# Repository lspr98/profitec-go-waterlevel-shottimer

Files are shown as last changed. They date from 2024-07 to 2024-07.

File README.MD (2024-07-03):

# Waterlevel-indicator and shot-timer for the Profitec GO

<p align="middle">
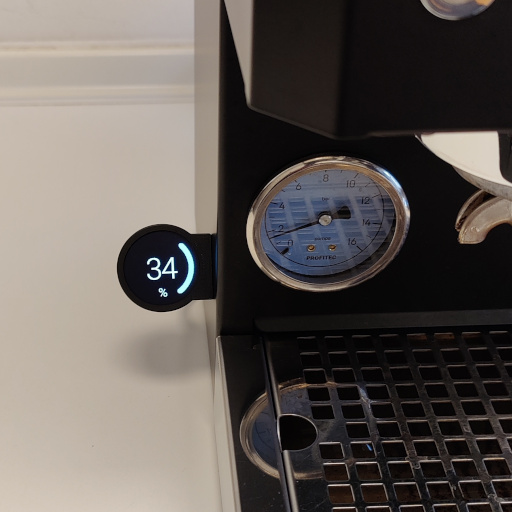
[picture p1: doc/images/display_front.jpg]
  
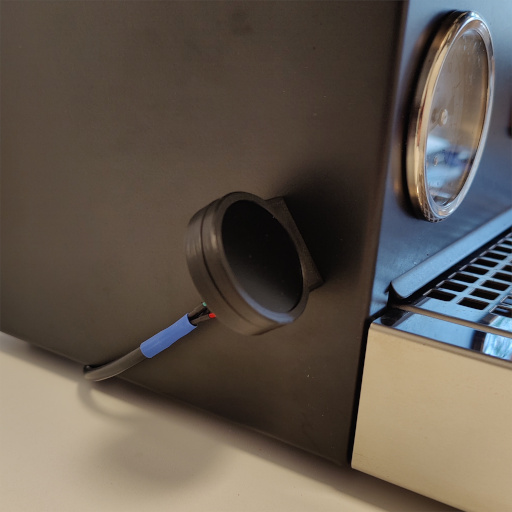
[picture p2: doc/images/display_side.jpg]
   
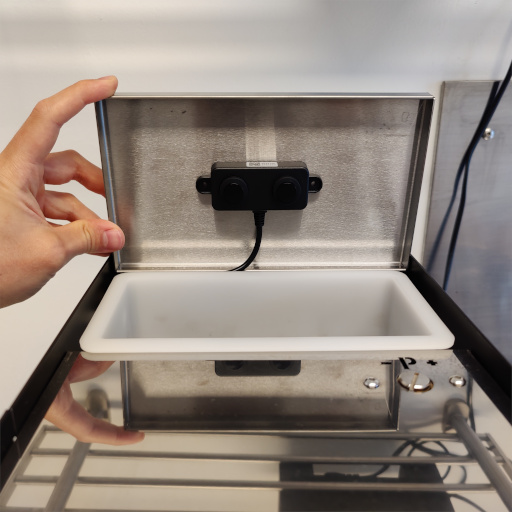
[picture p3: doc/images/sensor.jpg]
  
</p>

A modern display mod for espresso machines with vibrationpumps. Includes a shot-timer and waterlevel-indicator. Uses an accelerometer to detect vibrations for waking-up the display and timing shots. Measures and displays the waterlevel based on a contactless ultrasonic sensor. Attaches to the machine via a magnet for easy repositioning. The mod was originally developed and tested for the Profitec GO, however, other machines with vibrationpumps might work as well.

## Features
|Tap wake|Portafilter wake|Timer|
|---|---|---|
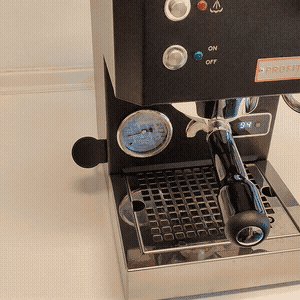
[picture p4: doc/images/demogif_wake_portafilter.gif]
||||

- contactless waterlevel measurement
- easy repositioning via magnetic attachment
- automatic wake when interacting with the machine
- automatic shot-timer
- non-destructive installation, minimal wiring outside the machine
- adjustable colors, sensitivity, etc...

## Disclaimer and warning
Recreating this project involves handling dangerous things like soldering irons, 3D-printers and mains voltage. For legal reasons, handling these things should only be done by an expert. I am not responsible for any damage to you, your machine or your surrounding. Read through the complete [manual](doc/manual/manual.pdf) to decide if you feel comfortable building the mod and if it is worth the effort to you.

## Required Tools
- 3D-printer
- soldering iron
- connector crimping kit (see BoM)

## Building Instructions
The building manual can be found [here](doc/manual/manual.pdf)

## Usage notes and configuration
I unfortunately don't have a second machine to test how well the settings transfer to different machines, so here are some hints on how to dial in things like detection sensitivity and timings. All relevent parameters (**highlighted in bold**) can be adjusted in [include/config.h](include/config.h). You need to reflash the firmware after making any changes. Refer to the manual on how to flash the firmware. **Never connect to the display via USB when the display cable is plugged in to avoid damage to your computer.** The 5V lines of the USB port and the display cable are connected!

### Adjusting vibration sensing sensitivity
The parameter for controlling vibration detection sensitivity is **WAKE_THRESH**. A lower value increases sensitivity, a higher value decreases sensitivity. The value has to be larger than 0. For different machines and mounting positions of the display, a different value for **WAKE_THRESH** may be required for reliable operation. The sensitivity affects both, the wake and timer function. A good value for **WAKE_THRESH** should wake the display when gently tapping on it and should keep the timer going reliably. My method of deciding on the threshold: you should be able to wake the display by slamming your fist on the surface on which the machine is standing on but it should not wake when placing a glass of water on that surface.

### Adjusting waterlevel and warning threshold
A fill level of 0 percent is shown if the sensor reports a distance of **LEVEL_MAX_DIST_MM** millimeters or more. A fill level of 100 percent is shown if the sensor reports a distance of **LEVEL_MIN_DIST_MM** millimeters or less. You can configure these two values to account for different watertank depths. The percentage below which the color of the ring will change to orange is configured with **LEVEL_BAD_PERC**.

### Shottimer
The shottimer is displayed with a delay of two seconds, which is on purpose. When a vibration is detected, the system will timeout for two seconds and check for a vibration after that timeout. If there is still a vibration, the timer starts (taking into account the time passed during the timeout). This is done to prevent the timer activating every time someone interacts with the machine. The delay can be configured via **TIMER_TRIGGER_DELAY_MS**. Setting this to zero will start the timer instantly when the display is awake and some vibration is detected. There is also the option to adjust *how many milliseconds one timer second has* via **TIMER_INCREMENT_MS**. I noticed that the timer on my machine seems to count a bit faster than a full second and verified that with the stopwatch of my smartphone. So you have that option to sync it with your machine timer.

### Deactivating waterlevel function or timer function
If you do not need the waterlevel but want the timer function, the system can be used without plugging in any levelsensor. The default wakescreen will be an orange ring with a questionmark, indicating a missing sensor. If you don't want the shottimer function, you can deactivate it by setting **ENABLE_TIMER** to false.

## Bill of materials (BoM)

The following items are necessary to build the waterlevel indicator. Items marked with a (*) at the beginning do not need to be the exact listed item but may be replaced with something else. Sourcing links are included for people based in germany (those are the shops where I got the items from).

|Item|Amount|Description|Comment|Sourcing (DE)|
|---|---|---|---|---|
|Waveshare RP2040-LCD-1.28|1|3-in-1 display, IMU and microcontroller|-|[BerryBase](https://www.berrybase.de/rp2040-mcu-board-1-28-zoll-runde-lcd-beschleunigungssensor-und-gyroskop)|
|DFRobot A02YYUW|1|waterproof ultrasonic sensor to measure waterlevel|-|[BotLand](https://botland.de/ultraschall-abstandssensoren/15717-ultraschall-abstandssensor-a02yyuw-3-450cm-wasserdicht-dfrobot-sen0311-5904422377984.html)|
|4-core wire|~1m|wire between display, sensor and power supply|I recommend using any old USB cable which you don't need anymore. For the Profitec Go, the wire diameter has to be smaller than 6mm to fit through one of the holes in the bottom of the machine!|-|
|M3 screw|1|required to screw the two 3D-printed parts together|12mm length|-|
|M3 Nut|1|required to secure the M3 screw|-|-|
|*Meanwell LPV-20-5|1|power supply to convert mains voltage to 5V|any small 5V power supply capable of delivering more than 0.5W should work, make sure they have fault-protection and have sufficient IP classification. This one is overkill with 15W but leaves headroom for future mods|[Reichelt](https://www.reichelt.de/led-trafo-15-w-5-v-dc-3000-ma-mw-lpv-20-5-p185792.html?&trstct=pos_14&nbc=1)|
|*Disc neodym magnet 12mm x 5mm|1|-|a smaller magent also works as long as it is strong enough. The magnet compartment is 12mm in diameter and 5mm high.|[Maqna](https://www.maqna.de/neodym-scheibenmagnet-13x5mm-vernickelt-grade-n45)|
|*Tesa Powerbond doublesided tape|~15cm|used for mounting the ultrasonic sensor and 5V power supply to the machine|other doublesided tape works too, make sure it has some thickness to it, since the bottom surface of the sensor is slightly recessed|[Hornbach](https://www.hornbach.de/p/tesa-powerbond-montageband-ultra-strong-1-5m-x-19mm/8643115/)|
|*Dupont 2-Pin Male and Female connectors|2|connects the display unit to the sensor and power supply|4x 1-pin is also possible. Only the 1-pin and 2-pin connectors fit through the holes in the bottom of the Profitec GO (~6mm diameter). Note: the linked product includes the required crimping tools and also the JST-XH connectors listed next|[Amazon](https://www.amazon.de/SOMELINE%C2%AE-Crimpzange-Stecker-JST-XH-EI-Serie/dp/B0C8N8JBDC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)|
|*JST-XH 4-Pin Male and Female connectors|2|connectors for display unit and sensor unit|other 4-pin connectors are also possible, but the 3D-printed parts are designed to house a JST-XH 4-Pin Female port.|see Dupont connectors|
|*JST-XH 2-Pin Male and Female connectors|1|connector for wiring harness and power supply|other 2-pin connectors are also possible|see Dupont connectors|
|*Wago 221-413 splicing connector|2|used to hook into the 230V line and connect the 5V power supply|it is also possible to instead build Y-splitters with connectors that are compatible with your machine to have a non-destructive installation|[Hornbach](https://www.hornbach.de/p/wago-221-413-compact-verbindungsklemme-0-14-4mm-3-leiter-hebelklemme-12-stueck/10593116/)|

Apart from the items listed above, you will need common consumables like **shrink tubing, solder and 3D-printer filament**.

It is also possible to connect the display, sensor and power supply by directly soldering the wires together if you do not want to buy and crimp any connectors. In this case, you won't be able to detach the display or sensor without cutting the wires.

### Support me
If you want to give something back, you can download the **.stl** models for 3D-printing from my [Printables project](https://www.printables.com/de/model/931582-profitec-go-waterlevel-indicator-with-shot-timer) to help me fill my Prusameters. Thank you :)

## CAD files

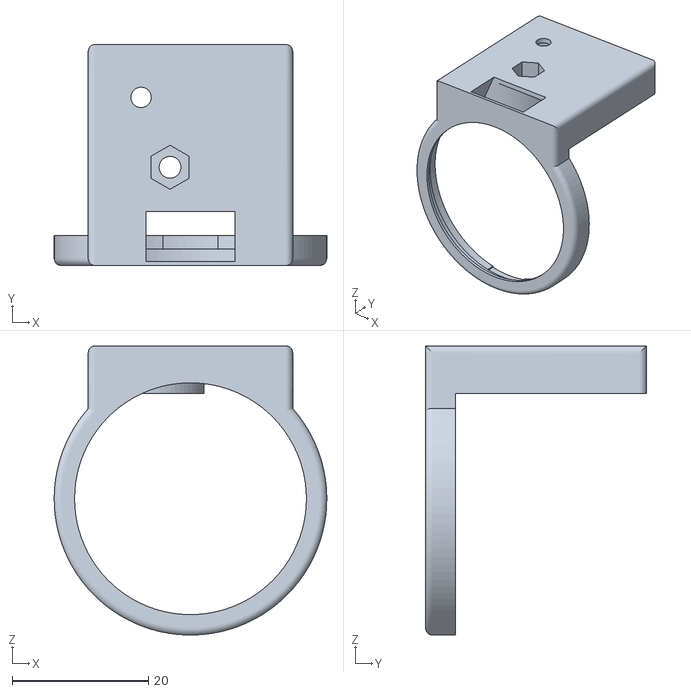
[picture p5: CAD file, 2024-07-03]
hardware/Frame v14.stl
40.0 x 32.4 x 42.4

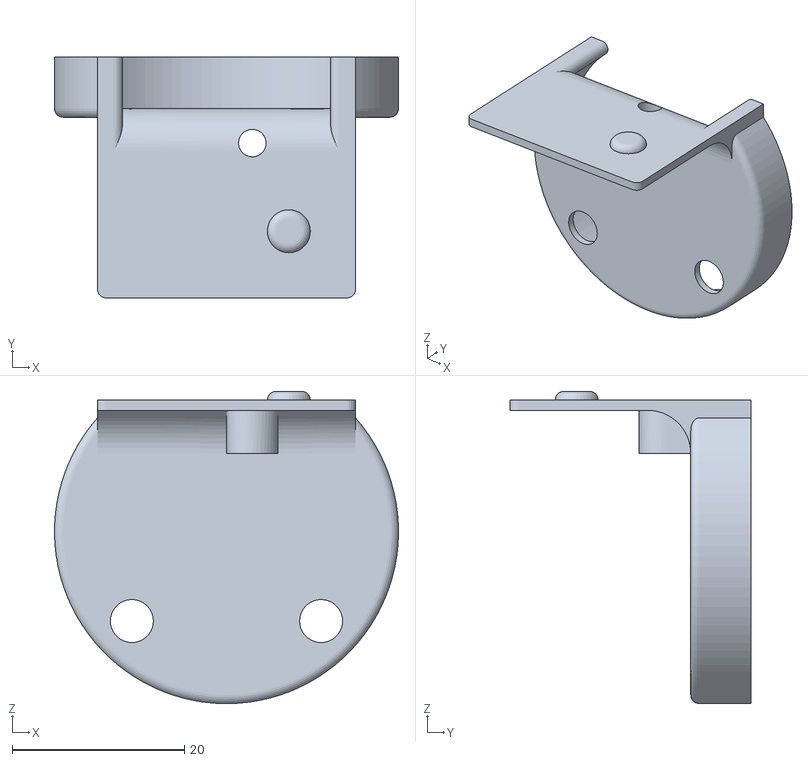
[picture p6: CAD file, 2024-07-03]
hardware/Lid v10.stl
40.0 x 28.0 x 36.3

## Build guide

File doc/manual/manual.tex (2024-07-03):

\documentclass[]{article}

\usepackage{graphicx,wrapfig}

%opening
\title{Installation instructions}
\author{lspr98}

\begin{document}

\maketitle

\begin{abstract}
	This document guides you through the process of building and installing the mod into a Profitec GO machine. These instructions are just my recommendations of installing the mod. Please read through the whole document before starting the build, to see what awaits you. 
\end{abstract}

\section{}
\subsection{Building the display unit}
\subsubsection{Printing the housing}
\begin{minipage}[t]{0.5\linewidth}
	\vspace{0pt}
	Print the two \textbf{.stl} files in the hardware folder using a filament of your choice. Orient the parts as shown in the screenshot from PrusaSlicer. Set the \textbf{layer height to 0.2mm} and \textbf{enable support everywhere}.
\end{minipage}
\hfill
\begin{minipage}[t]{0.4\linewidth}
	\vspace{0pt}
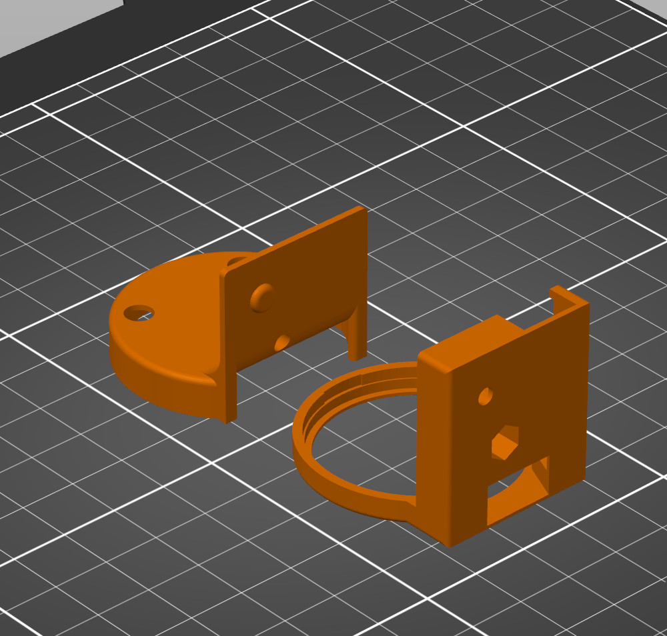
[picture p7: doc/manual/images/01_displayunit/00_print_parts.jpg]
	
\end{minipage}

\subsubsection{Preparing the LCD display}
\begin{minipage}[t]{0.5\linewidth}
	\vspace{0pt}
	Power up the RP2040-LCD-1.28 by plugging in a USB-C cable to confirm that it is working. It should come preloaded with a firmware that shows something on the screen. Do not peel off the screen protector yet. Take a set of tweezers and remove the two big black connectors at the back. Take something flat and sharp to gently pry the black plastic part up (there is a little notch at the short side of the connectors). After the plastic parts are removed, carefully tear off the metal connectors.
\end{minipage}
\hfill
\begin{minipage}[t]{0.4\linewidth}
	\vspace{0pt}
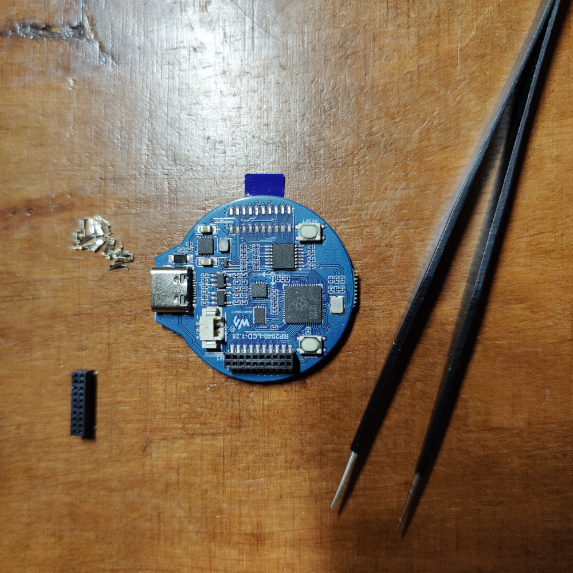
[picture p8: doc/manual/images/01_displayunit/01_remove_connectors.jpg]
	
\end{minipage}

\subsubsection{Preparing the display wires}
\begin{minipage}[t]{0.5\linewidth}
	\vspace{0pt}
	Cut 4 wires approximately 5cm in length. Remove the insulation of one end by around 2mm and by around 4mm at the other end for each wire. Twist all ends and apply solder.
\end{minipage}
\hfill
\begin{minipage}[t]{0.4\linewidth}
	\vspace{0pt}
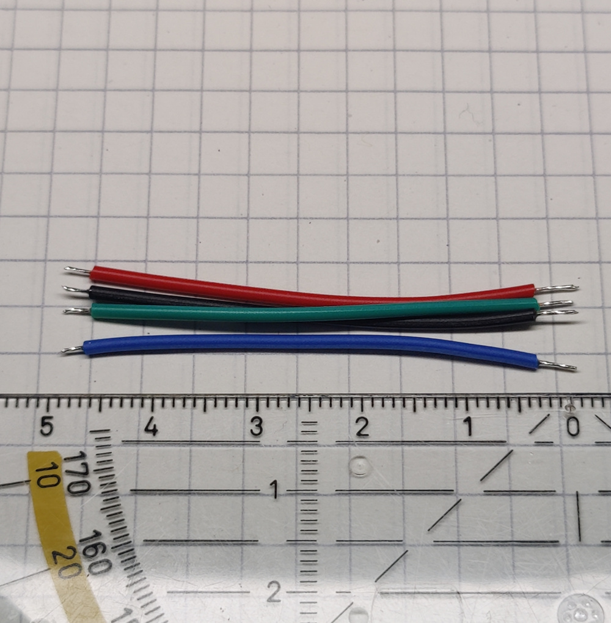
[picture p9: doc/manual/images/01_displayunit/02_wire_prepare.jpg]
	
\end{minipage}

\subsubsection{Tinning the required pads}
\begin{minipage}[t]{0.5\linewidth}
	\vspace{0pt}
	Apply a small amount of solder to the four pads highlighted in color. We will solder a wire to each of them in the next step. Be careful not to bridge any pads.
\end{minipage}
\hfill
\begin{minipage}[t]{0.4\linewidth}
	\vspace{0pt}
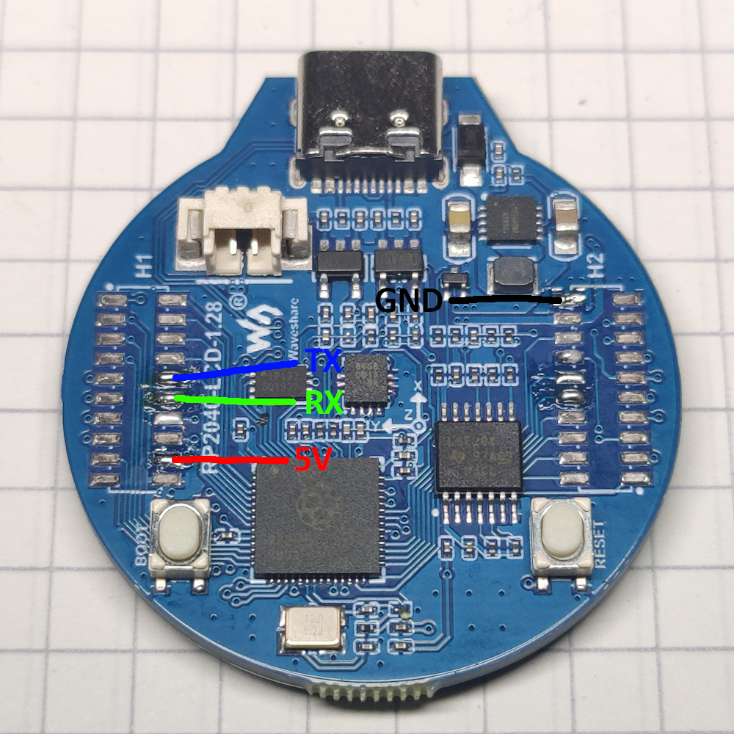
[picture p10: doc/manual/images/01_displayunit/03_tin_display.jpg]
	
\end{minipage}

\subsubsection{Soldering the wires to the display}
\begin{minipage}[t]{0.5\linewidth}
	\vspace{0pt}
	Solder the wires to the pads marked in the previous step.
\end{minipage}
\hfill
\begin{minipage}[t]{0.4\linewidth}
	\vspace{0pt}
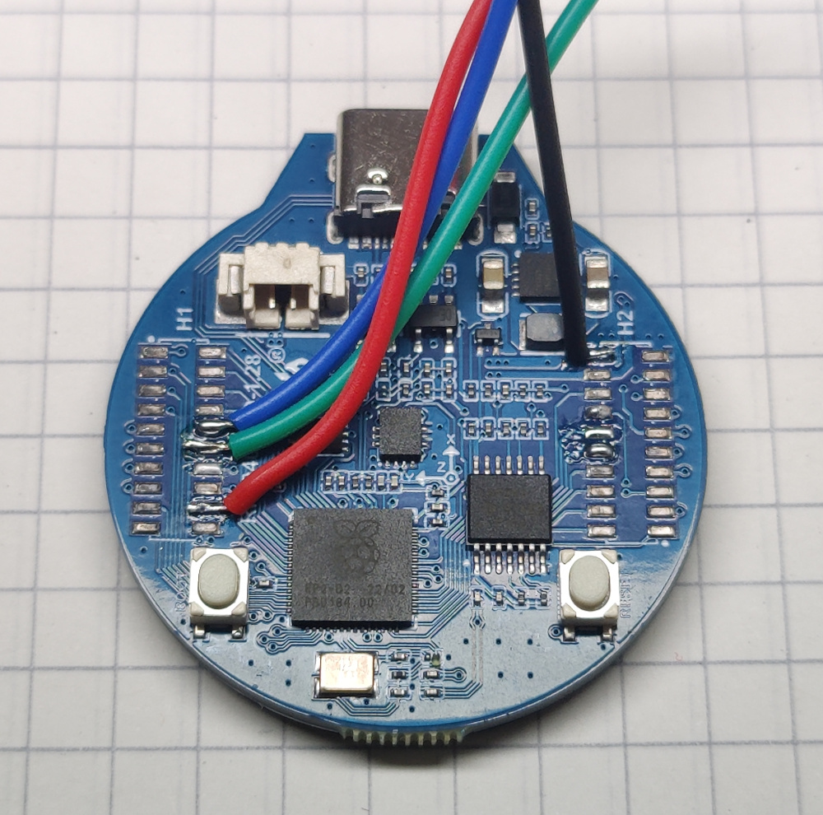
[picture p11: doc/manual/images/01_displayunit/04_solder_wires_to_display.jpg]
	
\end{minipage}

\subsubsection{Soldering the display plug}
\begin{minipage}[t]{0.5\linewidth}
	\vspace{0pt}
	Solder the other end of the wires to a JST-XH 4-Pin female connector. Make sure to put shrink tubing over the wires before attaching the connector. Make sure the wires are attached in the correct order to the connector (compare image).
\end{minipage}
\hfill
\begin{minipage}[t]{0.4\linewidth}
	\vspace{0pt}
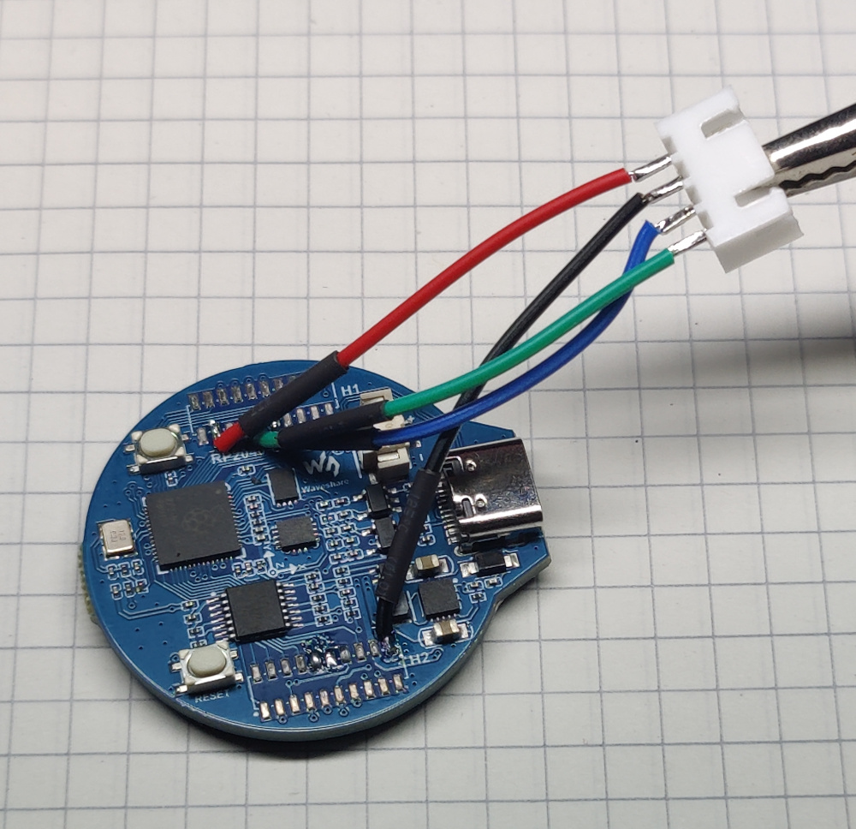
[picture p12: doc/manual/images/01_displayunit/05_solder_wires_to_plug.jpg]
	
\end{minipage}

\subsubsection{Applying the shrink tubing}
\begin{minipage}[t]{0.5\linewidth}
	\vspace{0pt}
	Push the shrink tubing over the uncovered wire ends and heat them up using a lighter. Do not heat up the connector too much, otherwise the pins may become lose as the plastic softens!
\end{minipage}
\hfill
\begin{minipage}[t]{0.4\linewidth}
	\vspace{0pt}
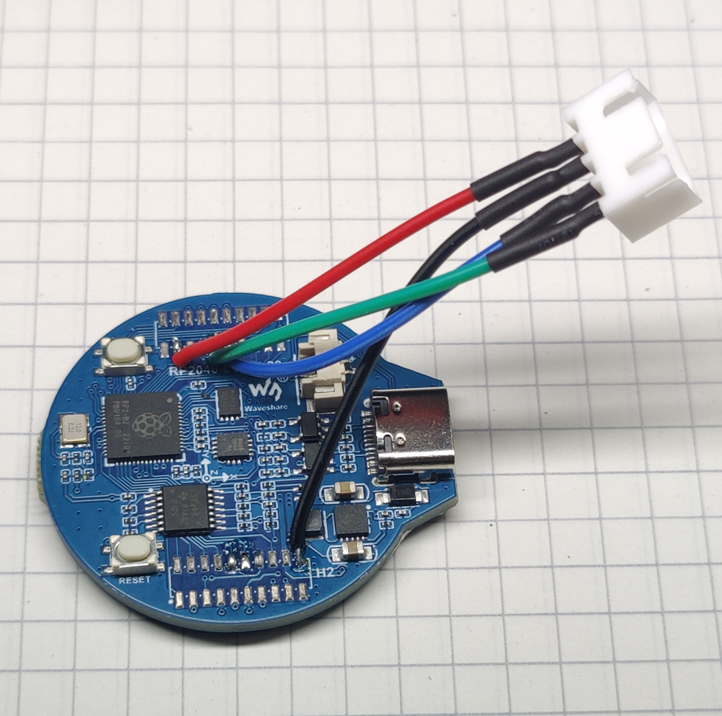
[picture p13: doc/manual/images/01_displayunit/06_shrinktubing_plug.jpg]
	
\end{minipage}

\subsubsection{Inserting the nut}
\begin{minipage}[t]{0.5\linewidth}
	\vspace{0pt}
	Take the M3 screw, the M3 nut and the 3d-printed Frame.stl part. Push the M3 screw through the hole that has a nut compartment at the other side. If the screw doesn't go through easily, take a screwdriver and screw it in completely. Screw on the nut onto the screw from the other side until it aligns with the surface of the 3D-printed part.
\end{minipage}
\hfill
\begin{minipage}[t]{0.4\linewidth}
	\vspace{0pt}
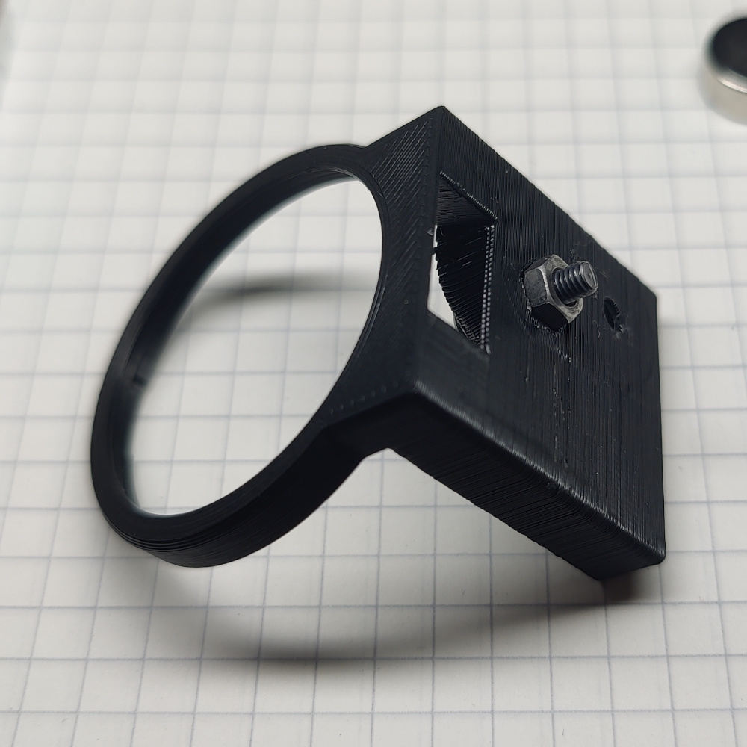
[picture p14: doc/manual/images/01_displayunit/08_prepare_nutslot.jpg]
	
\end{minipage}

\subsubsection{Pulling the nut in}
\begin{minipage}[t]{0.5\linewidth}
	\vspace{0pt}
	Keep screwing the M3-screw to pull the nut into the compartment until it is fully inserted (you can feel a sudden resistance when screwing). Do not apply too much force to avoid breaking the part. Remove the screw afterwards.
\end{minipage}
\hfill
\begin{minipage}[t]{0.4\linewidth}
	\vspace{0pt}
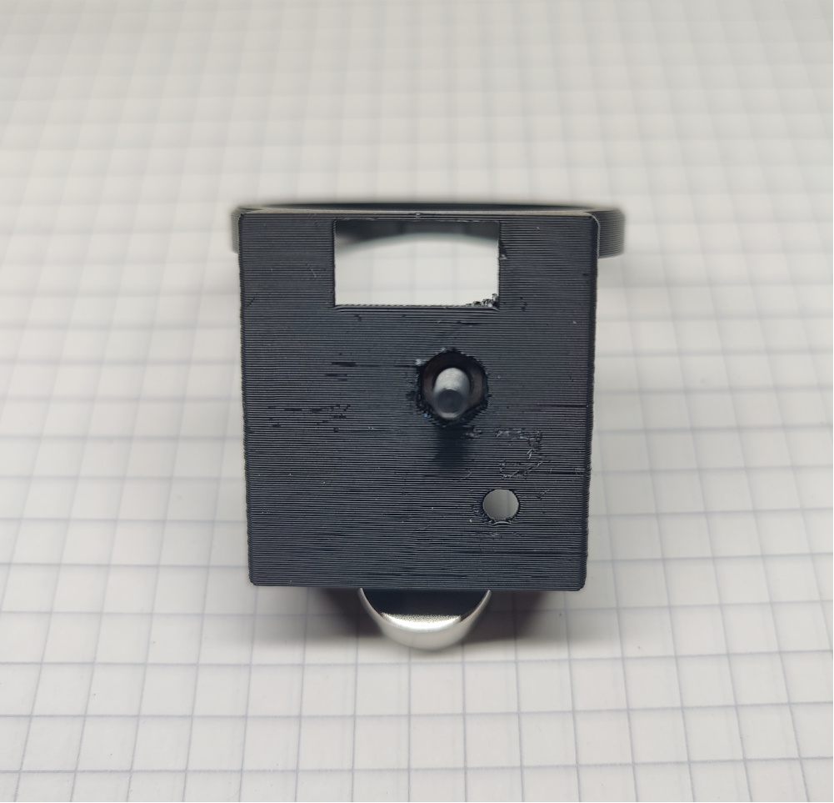
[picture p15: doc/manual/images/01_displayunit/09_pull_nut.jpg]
	
\end{minipage}

\subsubsection{Inserting the magnet}
\begin{minipage}[t]{0.5\linewidth}
	\vspace{0pt}
	Insert the magnet. If you use a smaller one, make sure you fix the magnet in place with glue or something. It should not be able to move afterwards. Make sure the magnet is fully inserted.
\end{minipage}
\hfill
\begin{minipage}[t]{0.4\linewidth}
	\vspace{0pt}
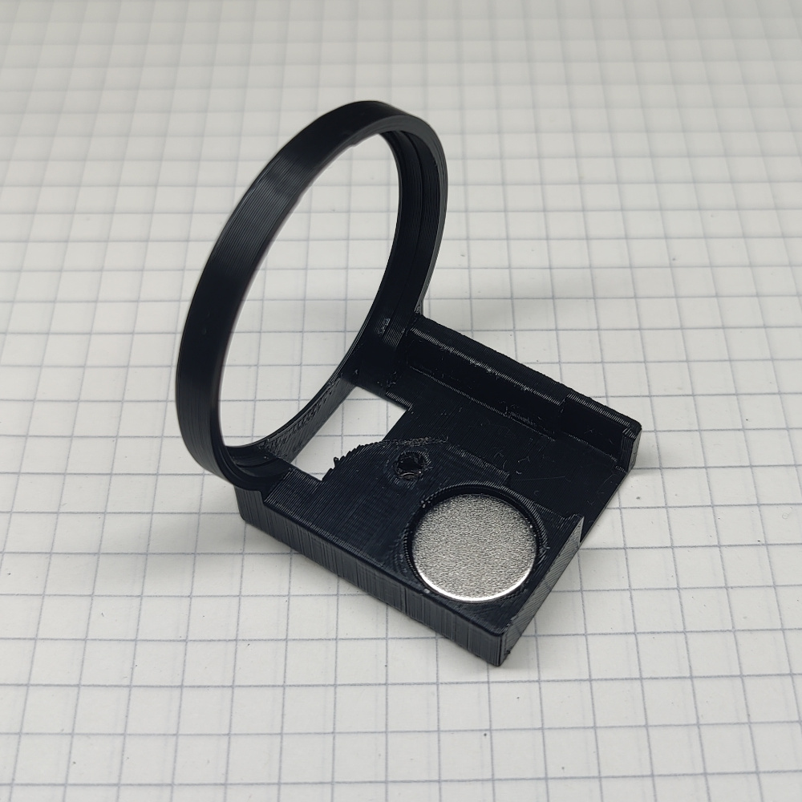
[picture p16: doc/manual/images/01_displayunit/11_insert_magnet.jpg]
	
\end{minipage}

\subsubsection{Aligning the display}
\begin{minipage}[t]{0.5\linewidth}
	\vspace{0pt}
	Carefully insert the display into the frame at an angle like shown in the picture. Then push it completely into the frame. It should snap in place without much force.
\end{minipage}
\hfill
\begin{minipage}[t]{0.4\linewidth}
	\vspace{0pt}
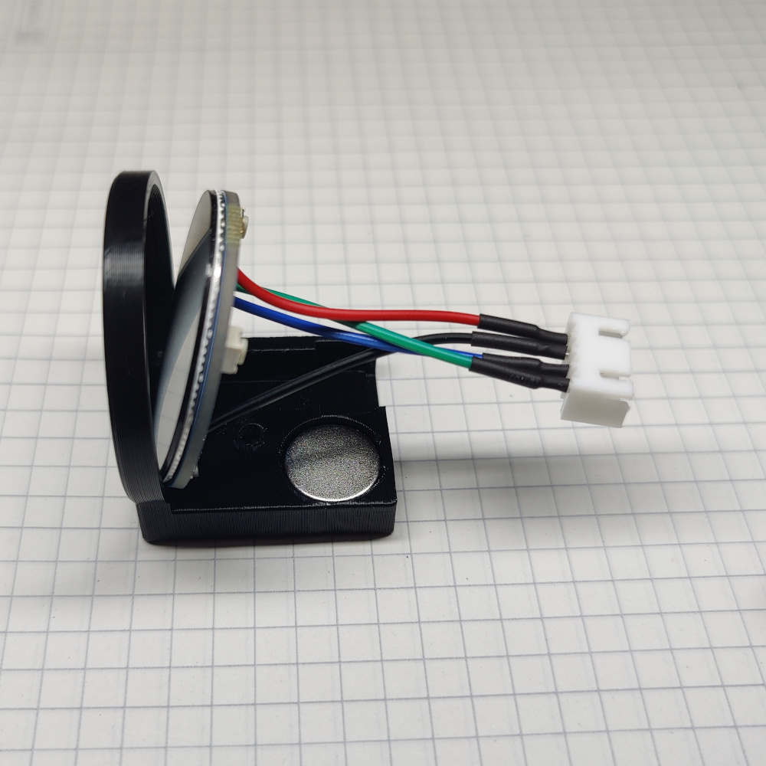
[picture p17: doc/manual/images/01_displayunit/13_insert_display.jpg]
	
\end{minipage}

\subsubsection{Checking display alignment}
\begin{minipage}[t]{0.5\linewidth}
	\vspace{0pt}
	If the display is inserted correctly, the PCB surface should align with the surface of the 3d-printed part. If you are having trouble to align it, check the 3D-printed part for any remaining support structures that were not removed.
\end{minipage}
\hfill
\begin{minipage}[t]{0.4\linewidth}
	\vspace{0pt}
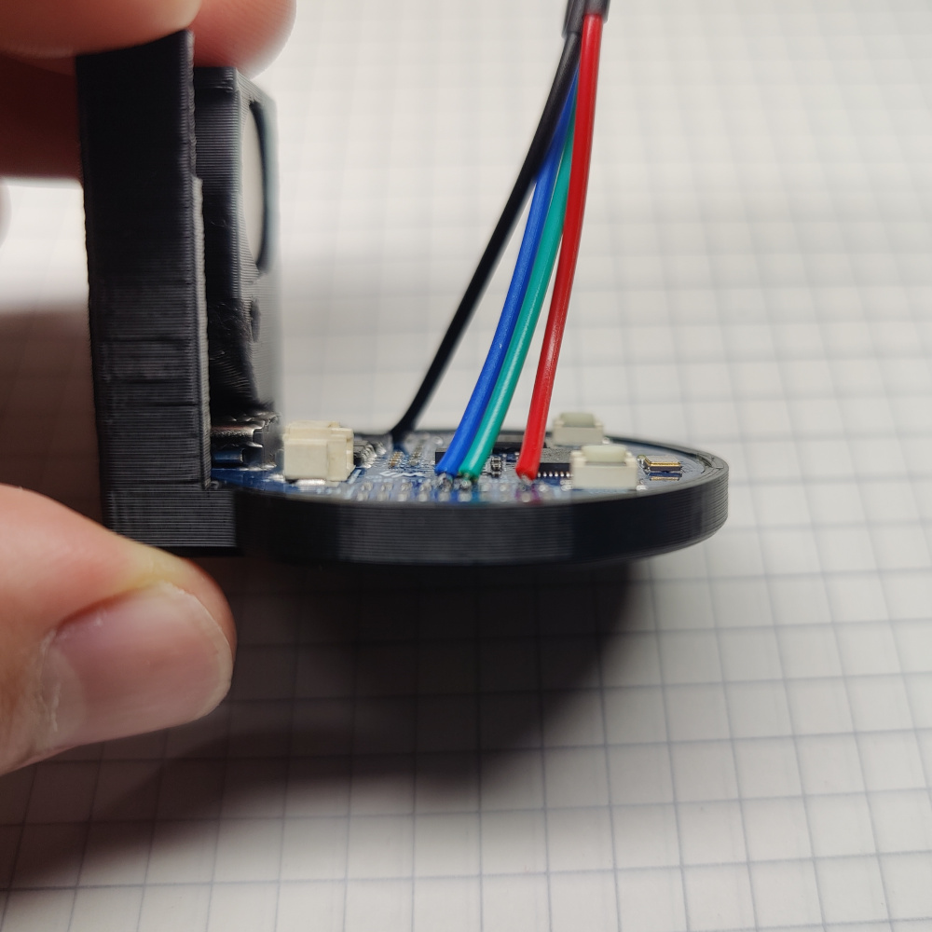
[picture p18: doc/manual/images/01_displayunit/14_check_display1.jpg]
	
\end{minipage}

\subsubsection{Checking USB-port alignment}
\begin{minipage}[t]{0.5\linewidth}
	\vspace{0pt}
	Verify that the USB-port at the bottom is fully accessible and not covered by the 3D-printed part.
\end{minipage}
\hfill
\begin{minipage}[t]{0.4\linewidth}
	\vspace{0pt}
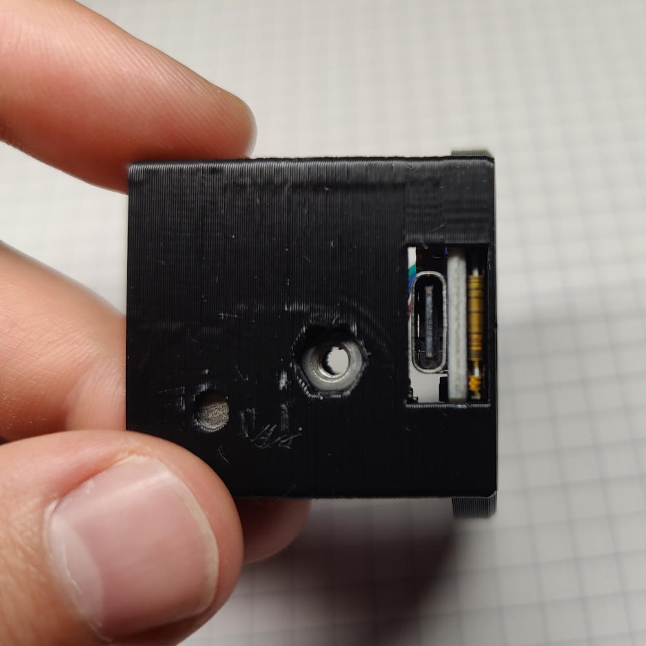
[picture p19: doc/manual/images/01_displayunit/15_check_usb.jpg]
	
\end{minipage}

\subsubsection{Inserting the display plug}
\begin{minipage}[t]{0.5\linewidth}
	\vspace{0pt}
	Push the JST-XH 4-Pin female connector into it's slot.
\end{minipage}
\hfill
\begin{minipage}[t]{0.4\linewidth}
	\vspace{0pt}
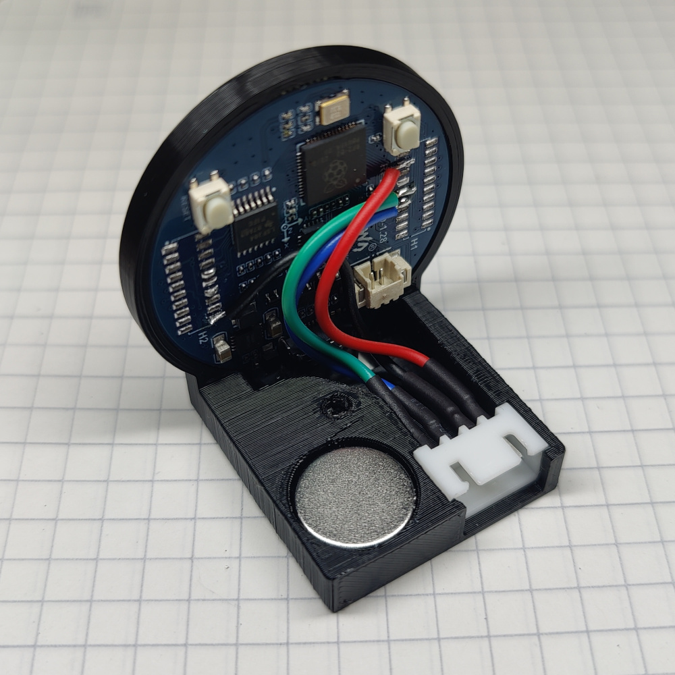
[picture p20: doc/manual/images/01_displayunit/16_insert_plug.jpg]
	
\end{minipage}

\subsubsection{Closing the frame}
\begin{minipage}[t]{0.5\linewidth}
	\vspace{0pt}
	Take the other 3D-printed part and close the frame by screwing the M3-screw in like shown in the picture. Be careful not to pinch any wires while doing so.
\end{minipage}
\hfill
\begin{minipage}[t]{0.4\linewidth}
	\vspace{0pt}
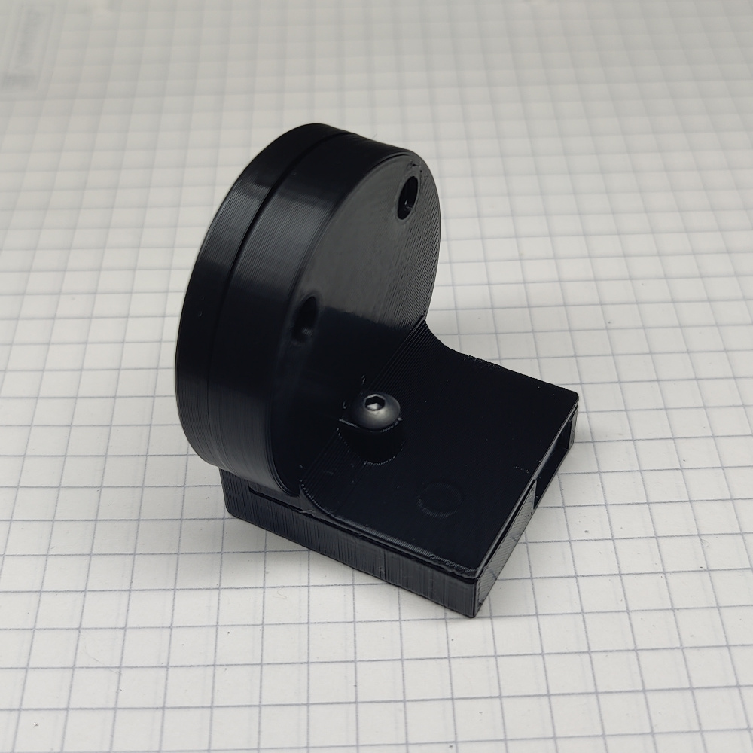
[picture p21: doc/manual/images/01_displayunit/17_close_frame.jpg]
	
\end{minipage}

\subsubsection{Checking the gaps}
\begin{minipage}[t]{0.5\linewidth}
	\vspace{0pt}
	If everything was done correctly, the two pieces should align, leaving (almost) no gap.
\end{minipage}
\hfill
\begin{minipage}[t]{0.4\linewidth}
	\vspace{0pt}
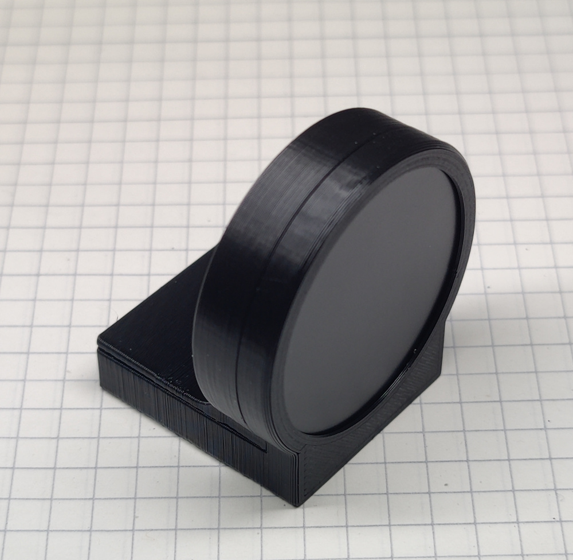
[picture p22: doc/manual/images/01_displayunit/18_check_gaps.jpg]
	
\end{minipage}

\subsubsection{Checking the buttons}
\begin{minipage}[t]{0.5\linewidth}
	\vspace{0pt}
	Verify that the two buttons at the back of the display are not covered or pushed by any wires and that no pins of the connector are bent.
\end{minipage}
\hfill
\begin{minipage}[t]{0.4\linewidth}
	\vspace{0pt}
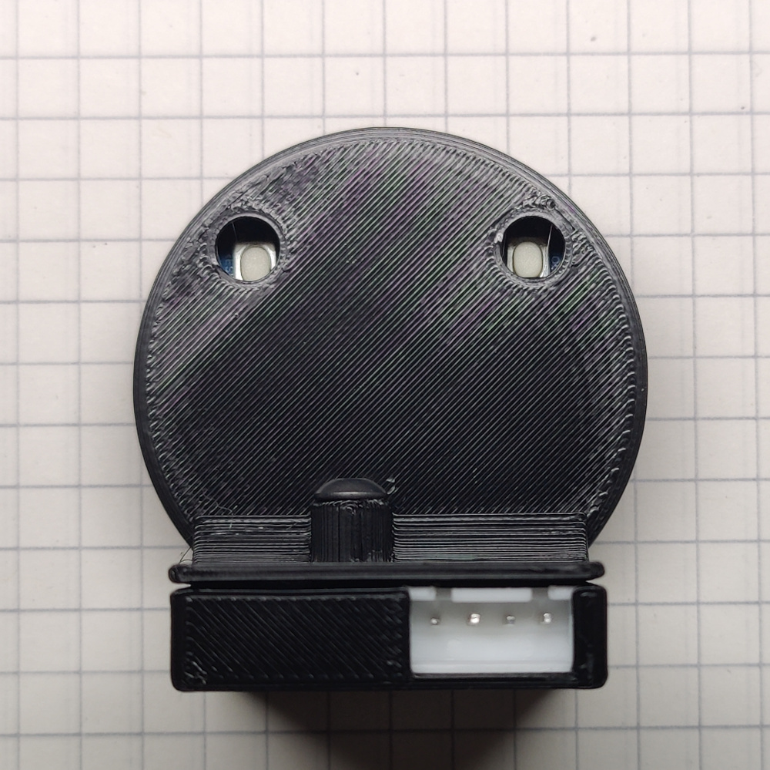
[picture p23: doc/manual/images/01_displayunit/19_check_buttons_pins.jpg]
	
\end{minipage}

\subsubsection{Checking the bottom}
\begin{minipage}[t]{0.5\linewidth}
	\vspace{0pt}
	Make sure no metal parts are sticking out from the bottom! The USB-port, the nut and the screw should be recessed to avoid scratching the surface of your machine.
\end{minipage}
\hfill
\begin{minipage}[t]{0.4\linewidth}
	\vspace{0pt}
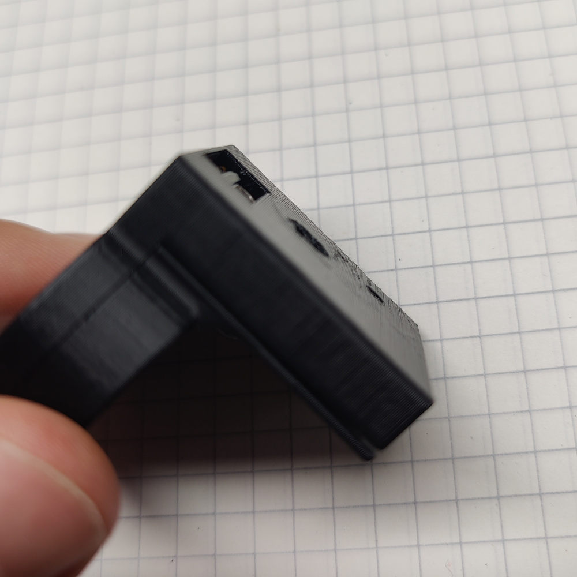
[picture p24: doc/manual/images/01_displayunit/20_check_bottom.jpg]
	
\end{minipage}

\subsubsection{Flashing the firmware}
\begin{minipage}[t]{0.5\linewidth}
	\vspace{0pt}
	If not done already, install VisualStudio Code and install the PlatformIO plugin for it. Clone the Github repository to your PC and open it as a PlatformIO project. Connect the display unit to your PC via a USB cable. Build and flash the firmware by pressing the highlighted button at the bottom left of the window.
\end{minipage}
\hfill
\begin{minipage}[t]{0.4\linewidth}
	\vspace{0pt}
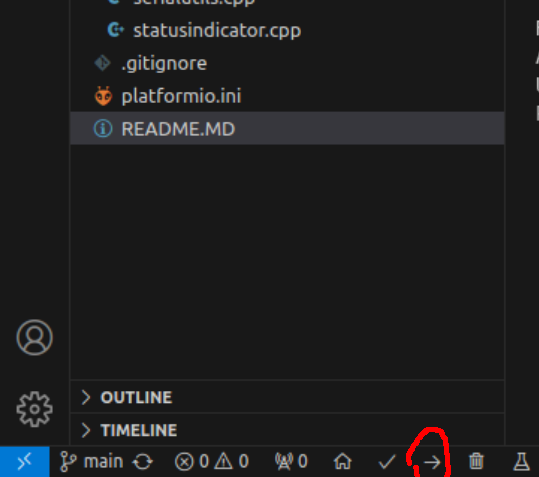
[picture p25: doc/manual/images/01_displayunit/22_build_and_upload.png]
	
\end{minipage}

\subsubsection{Testing}
\begin{minipage}[t]{0.5\linewidth}
	\vspace{0pt}
	If the flashing process was successful, it should show an orange ring with a question mark indicating a missing fill-level sensor. Try shaking the device for more than 2 seconds to test the shot timer.
\end{minipage}
\hfill
\begin{minipage}[t]{0.4\linewidth}
	\vspace{0pt}
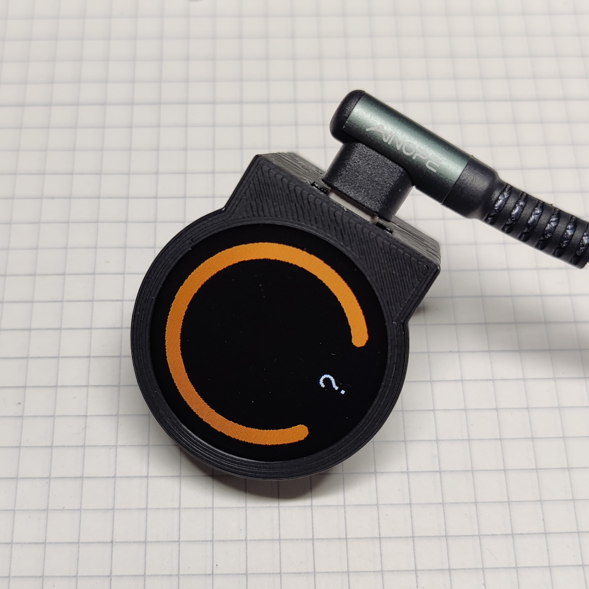
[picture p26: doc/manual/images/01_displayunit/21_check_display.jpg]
	
\end{minipage}

\subsection{Wire harness, level sensor and power supply}
\subsubsection{Display cable}
\begin{minipage}[t]{0.5\linewidth}
	\vspace{0pt}
	Take the old USB cable / your 4-core wire and cut it to around 40cm length. Strip the 4 wires in the cable and crimp a JST-XH 4-Pin male connector to one end and 2 2-Pin male Dupont connectors to the other end. One 2-Pin connector should have ground (GND) and 5V, the other should have RX the TX when the other end is connected to the display unit. For the Profitec GO, the cable has to fit through a 6mm diameter hole, hence 2 2-Pin Dupont connectors were used. Don't forget shrink tubing.
\end{minipage}
\hfill
\begin{minipage}[t]{0.4\linewidth}
	\vspace{0pt}
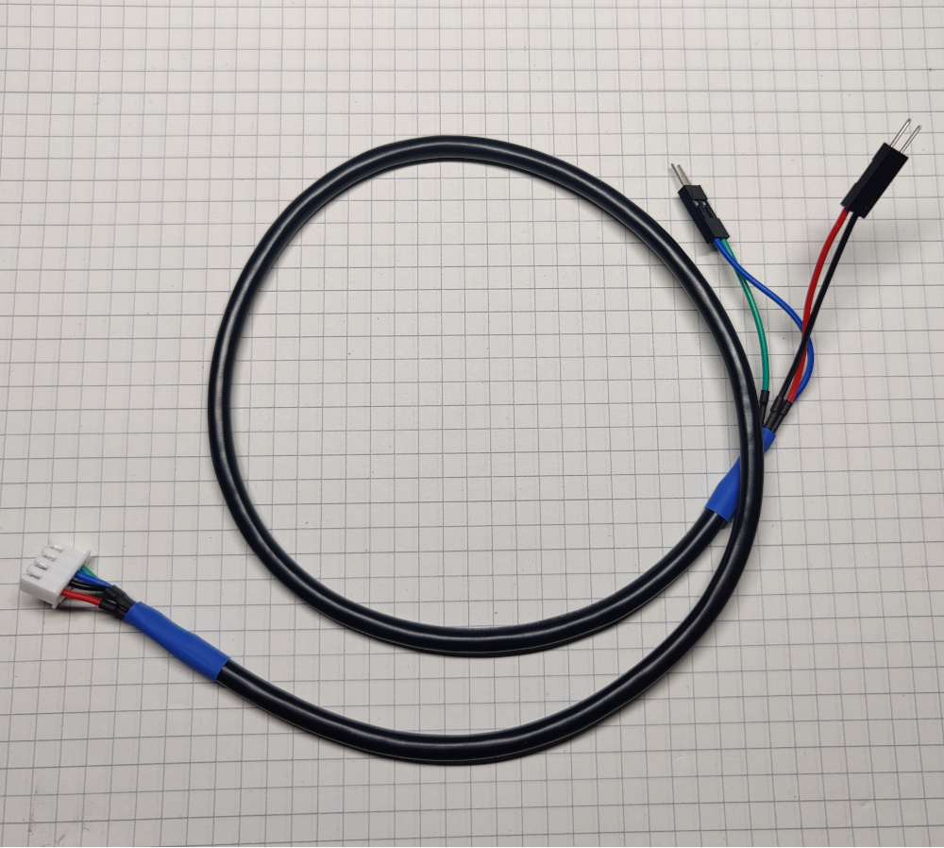
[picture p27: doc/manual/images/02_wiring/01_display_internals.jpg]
	
\end{minipage}

\subsubsection{Changing the level sensor plug}
\begin{minipage}[t]{0.5\linewidth}
	\vspace{0pt}
	Cut off the default plug of the A02YYUW ultrasonic sensor. Replace it with a JST-XH 4-Pin female connector. Pay attention to the color order. Don't forget shrink tubing.
\end{minipage}
\hfill
\begin{minipage}[t]{0.4\linewidth}
	\vspace{0pt}
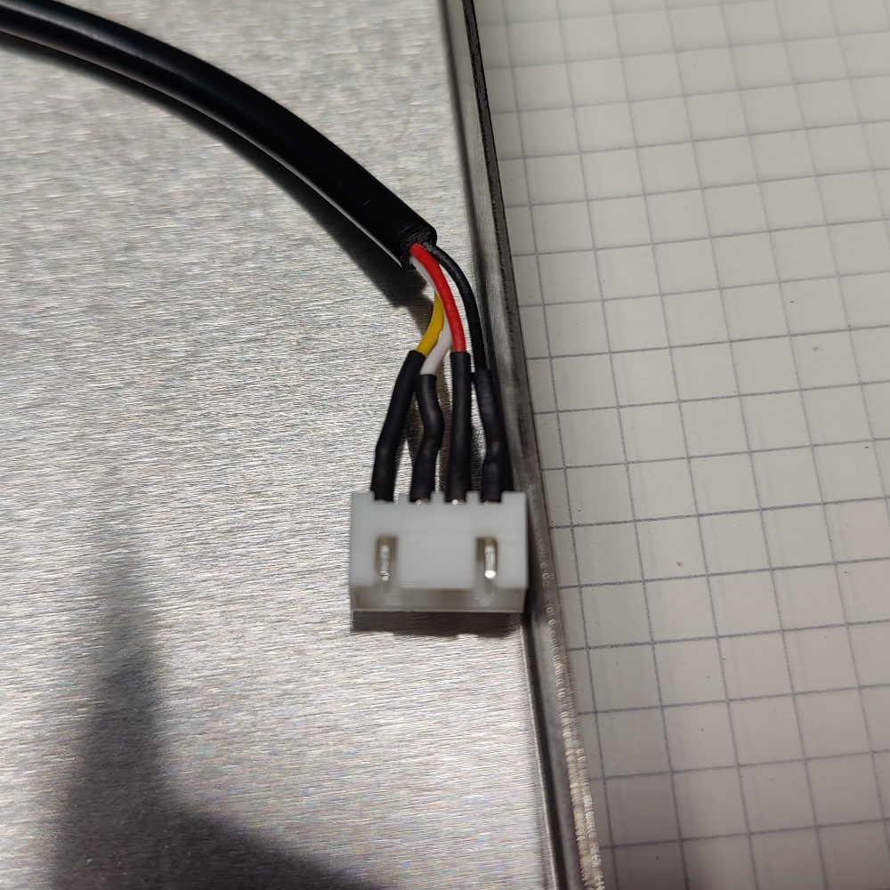
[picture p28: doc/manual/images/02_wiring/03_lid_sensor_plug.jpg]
	
\end{minipage}

\subsubsection{Attaching the level sensor plug}
\begin{minipage}[t]{0.5\linewidth}
	\vspace{0pt}
	Remove the water tank cover of your machine. Use the double-sided tape to stick the sensor to the bottom of the lid. Position the sensor such that it sits in the middle over the water area of the tank. For the Profitec GO, this means positioning the sensor in the middle of the lid.
\end{minipage}
\hfill
\begin{minipage}[t]{0.4\linewidth}
	\vspace{0pt}
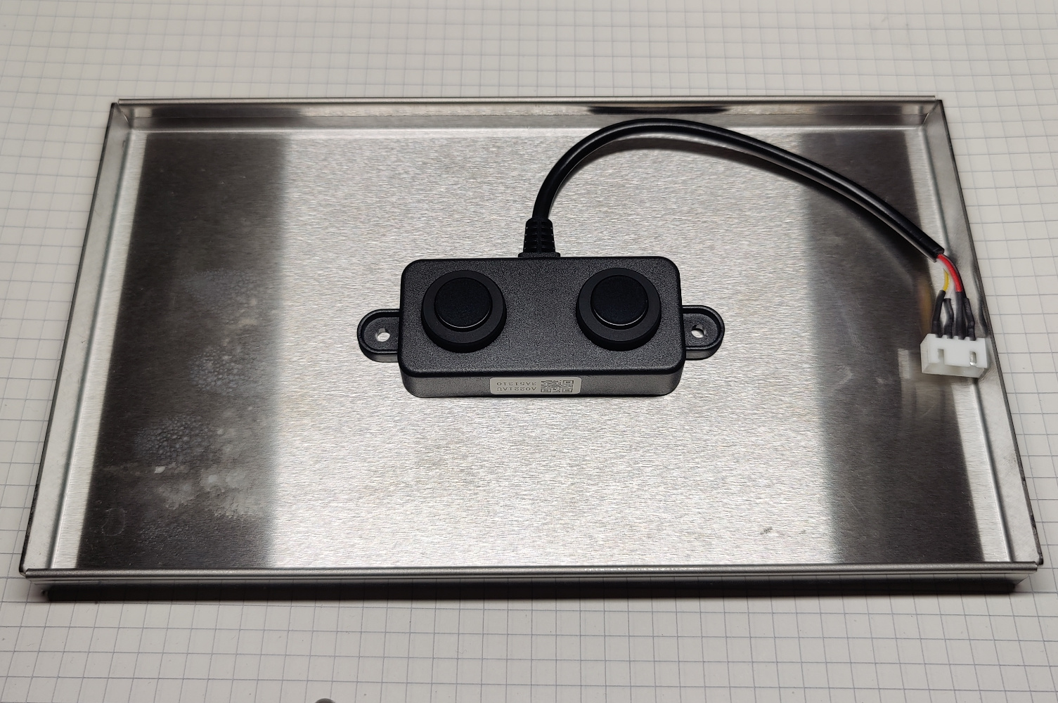
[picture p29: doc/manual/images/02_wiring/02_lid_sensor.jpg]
	
\end{minipage}

\subsubsection{Wiring harness}
\begin{minipage}[t]{0.5\linewidth}
	\vspace{0pt}
	Next, create a wiring harness that will connect the power supply, level sensor and the display unit. Create a Y-splitter for the red (5V) and black (ground) wires. Attach a JST-XH 2-Pin female connector to the two pole end (this will connect to the power supply). Attach a JST-XH 4-Pin male connector to one side of the 4-pole end and a 4-Pin female Dupont connector to the other 4-pole end. The 4-pole wire should be around 15cm long, the 2-pole wire around 20cm.
\end{minipage}
\hfill
\begin{minipage}[t]{0.4\linewidth}
	\vspace{0pt}
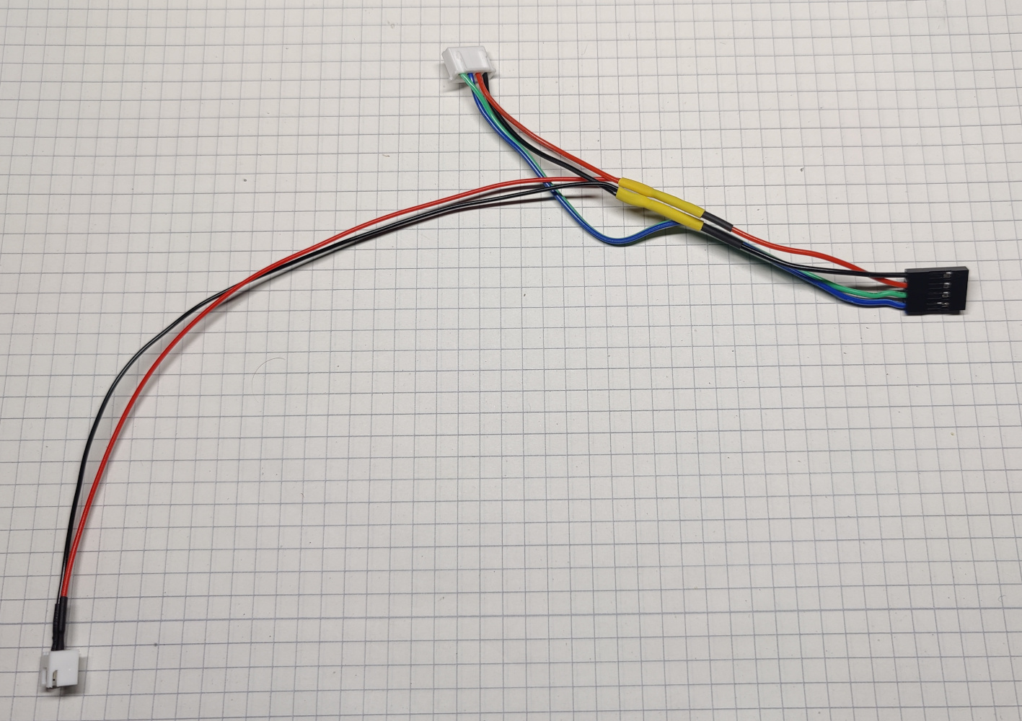
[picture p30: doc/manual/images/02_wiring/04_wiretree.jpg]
	
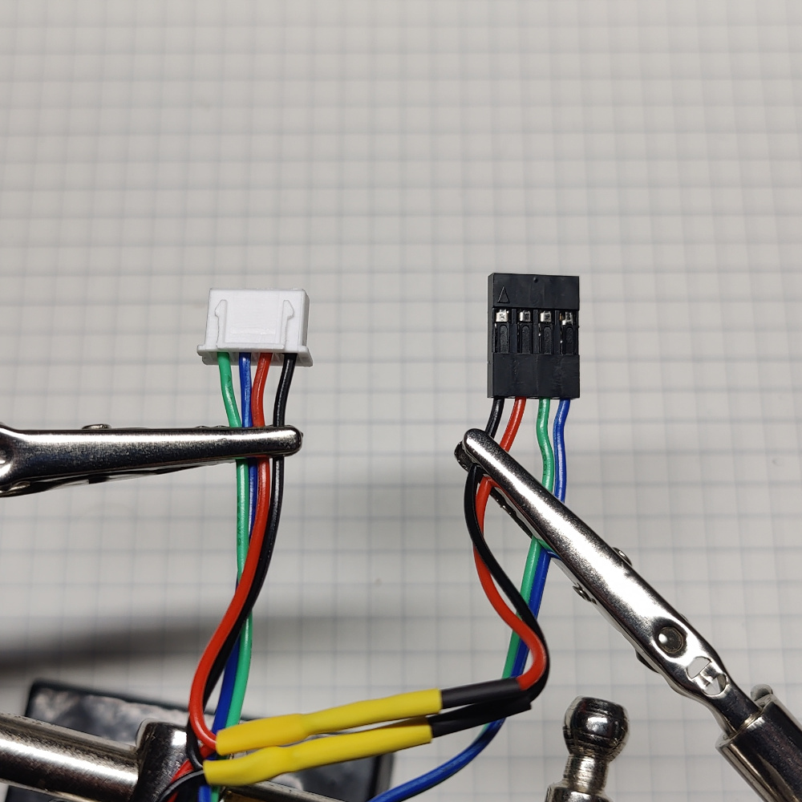
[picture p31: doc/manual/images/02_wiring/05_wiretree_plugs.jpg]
	
\end{minipage}

\subsubsection{Wiring harness connection check}
\begin{minipage}[t]{0.5\linewidth}
	\vspace{0pt}
	Plug the level sensor into the JST-XH 4-Pin connector of the wiring harness and plug the two 2-Pin Dupont connectors of the display cable into the 4-Pin Dupont of the wiring harness. Compare the colors of the wires to the picture to the right. Note that the blue and green wires are switched. That is because the RX-pin of the display needs to be connected to the TX-pin of the level sensor and vice-versa.
\end{minipage}
\hfill
\begin{minipage}[t]{0.4\linewidth}
	\vspace{0pt}
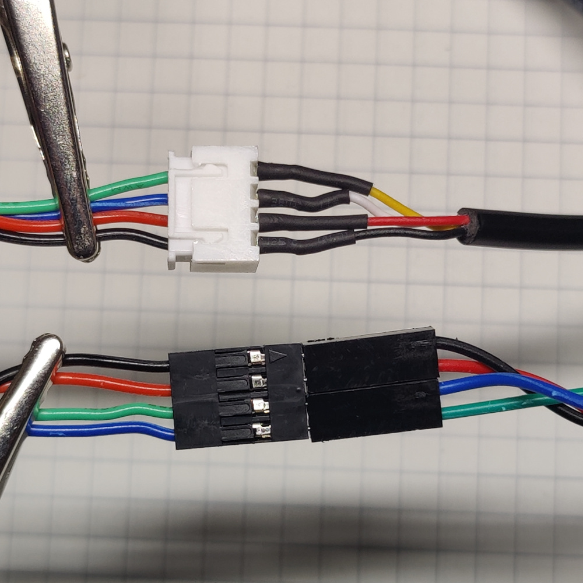
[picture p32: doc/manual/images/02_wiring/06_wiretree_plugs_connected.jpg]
	
\end{minipage}

\subsubsection{Power supply preparation}
\begin{minipage}[t]{0.5\linewidth}
	\vspace{0pt}
	Crimp a JST-XH 2-Pin male connector to the 5V output of your power supply. This will connect to the 2-Pin JST-XH of the wiring harness to supply the level sensor and display with power. If you want to use connectors compatible with your machine internal electronics, now is the time to crimp them to the power supply. I went with splicing connectors.
\end{minipage}
\hfill
\begin{minipage}[t]{0.4\linewidth}
	\vspace{0pt}
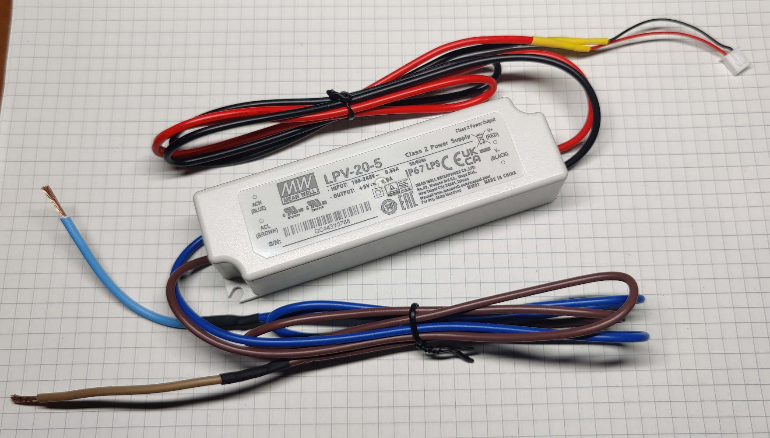
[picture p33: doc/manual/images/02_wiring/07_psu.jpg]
	
\end{minipage}

\subsubsection{Complete wiring overview and diagram}
\begin{minipage}[t]{0.5\linewidth}
	\vspace{0pt}
	The components connect together like shown in the picture. If you have a 5V lab power supply, feel free to power the system up to check that all connections are fine. Below is a sketch of the complete wiring. Make sure the components connect correctly.
\end{minipage}
\hfill
\begin{minipage}[t]{0.4\linewidth}
	\vspace{0pt}
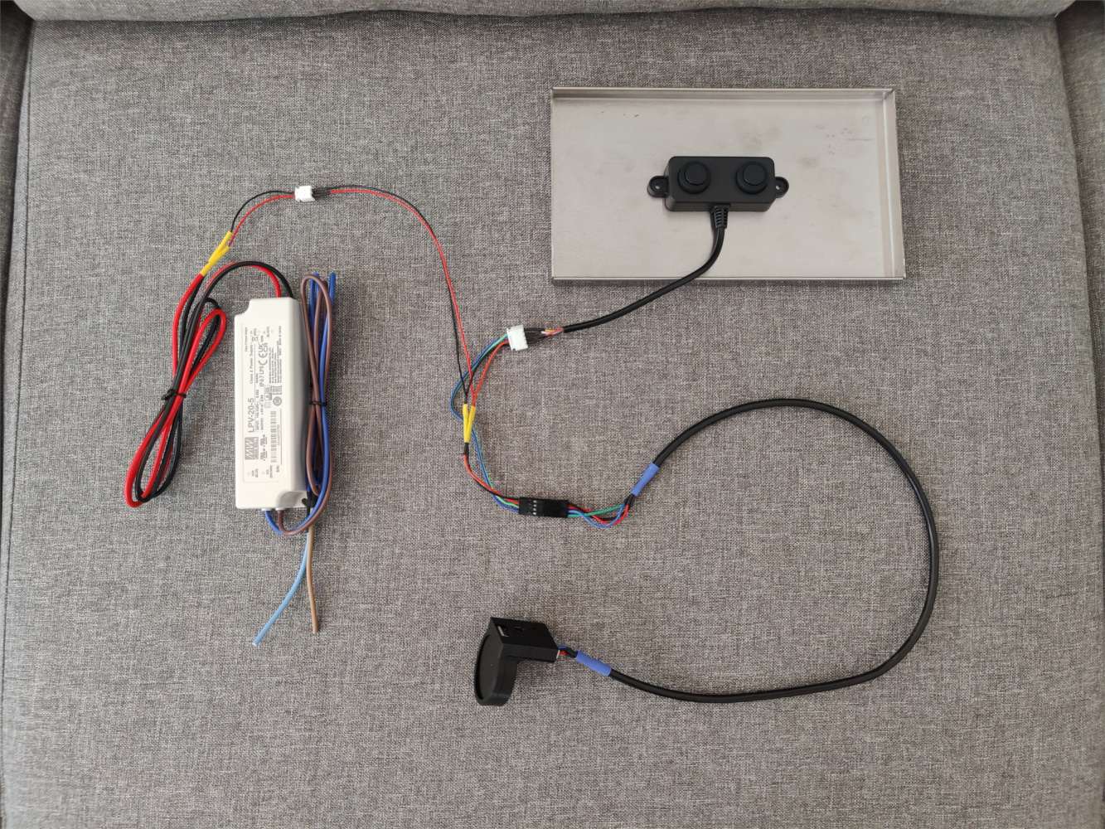
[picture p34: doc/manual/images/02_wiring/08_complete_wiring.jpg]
	
\end{minipage}
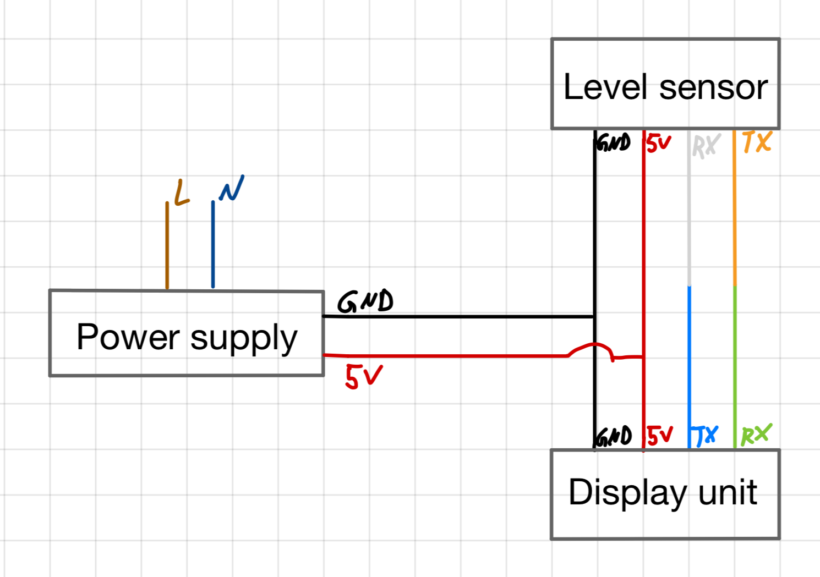
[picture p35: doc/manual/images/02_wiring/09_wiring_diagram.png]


\subsection{Machine installation}
This is your last chance to make a nice espresso before taking the machine apart. Use this opportunity to pull a shot that gets you through the remaining part of the installation :). \textbf{In this section, we will open the machine. There is the possibility to burn or shock yourself if you are not careful.} This section is specific to the Profitec GO, but you may use it as a reference for installation in a different machine.

\subsubsection{Preparation}
\begin{minipage}[t]{0.5\linewidth}
	\vspace{0pt}
	Remove the portafilter, water tray and \textbf{unplug the machine}. You may want to wait a few minutes for the machine to cool down before opening it up. 
\end{minipage}
\hfill
\begin{minipage}[t]{0.4\linewidth}
	\vspace{0pt}
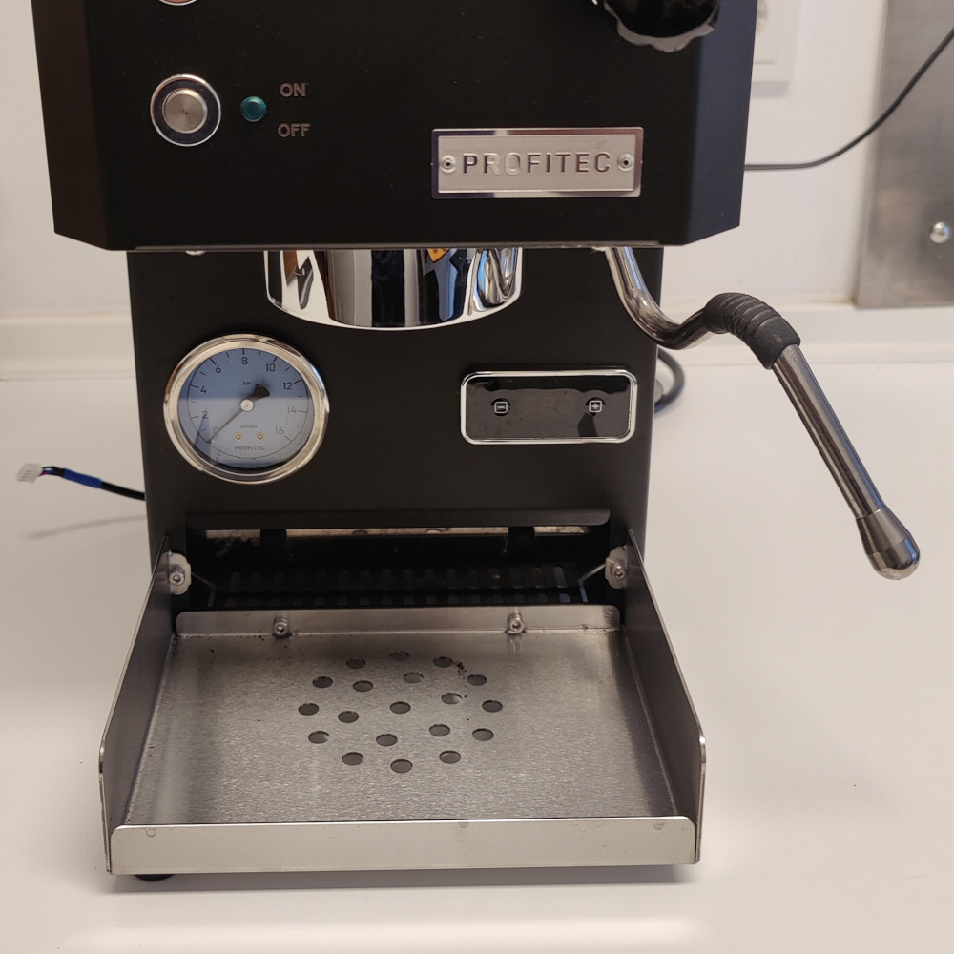
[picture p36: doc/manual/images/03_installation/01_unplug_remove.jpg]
	
\end{minipage}

\subsubsection{Removing the water tank}
\begin{minipage}[t]{0.5\linewidth}
	\vspace{0pt}
	Carefully pull out the water tank. When placing the water-tank onto a flat surface, I noticed that mine slowly leaks water with time. Hence, I recommend pouring the water in the tank into some other container.
\end{minipage}
\hfill
\begin{minipage}[t]{0.4\linewidth}
	\vspace{0pt}
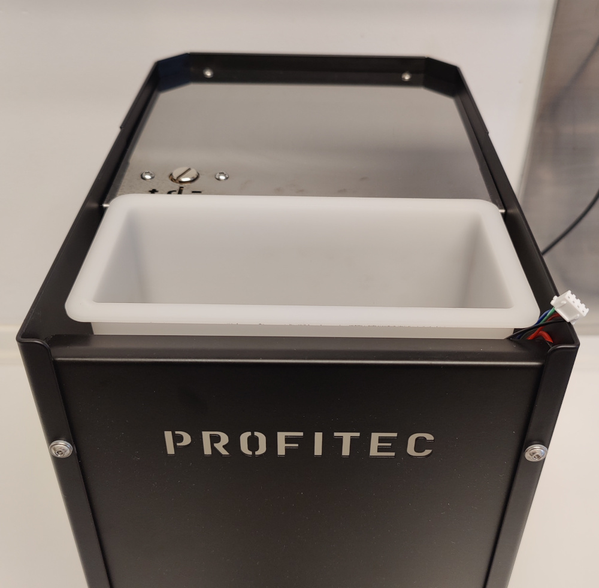
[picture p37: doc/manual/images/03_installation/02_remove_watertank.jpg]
	
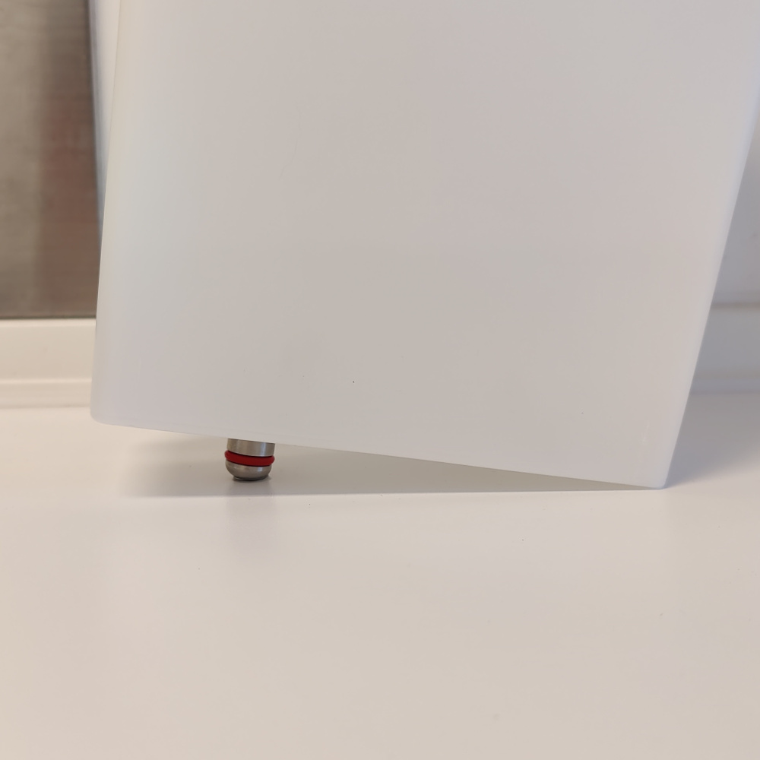
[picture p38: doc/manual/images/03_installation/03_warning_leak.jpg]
	
\end{minipage}

\subsubsection{Removing the backplate}
\label{sec:backplate}
\begin{minipage}[t]{0.5\linewidth}
	\vspace{0pt}
	\textbf{Verify that the machine is unplugged!} Unscrew the six screws on the back of the machine. Slide the backplate out upwards. Place it on some soft surface (e.g. a towel) to avoid scratches. Do NOT place any other parts we are about to remove on top of it.
\end{minipage}
\hfill
\begin{minipage}[t]{0.4\linewidth}
	\vspace{0pt}
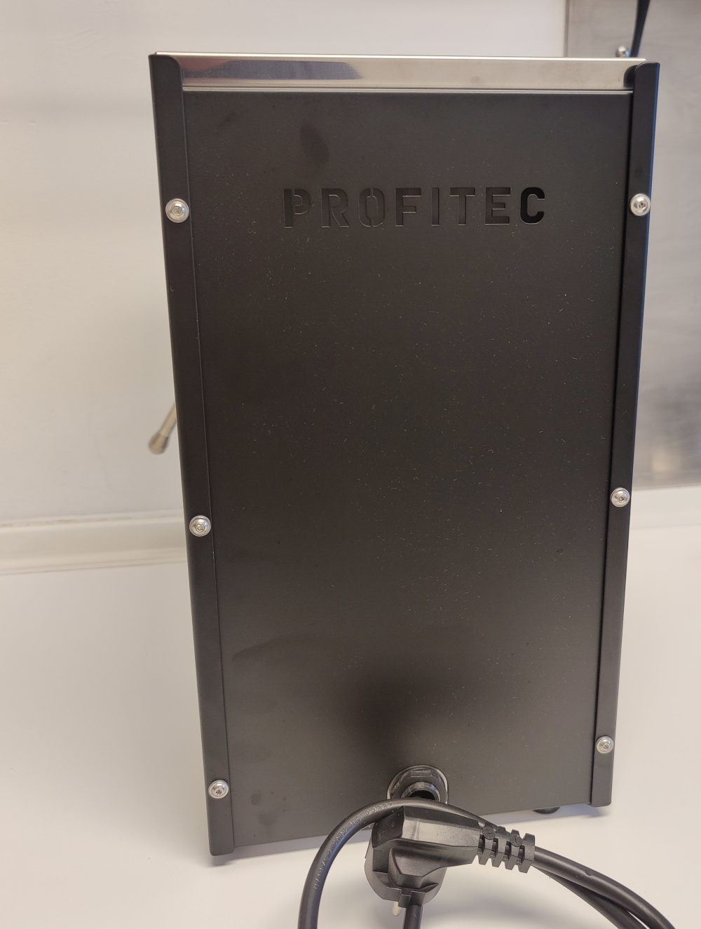
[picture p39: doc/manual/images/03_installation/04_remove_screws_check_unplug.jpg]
	
\end{minipage}

\subsubsection{Removing the topplate}
\label{sec:topplate}
\begin{minipage}[t]{0.5\linewidth}
	\vspace{0pt}
	Unscrew the six screws securing the topplate. Lift it up to remove it. Place it on some soft surface (e.g. a towel) to avoid scratches. Do NOT place any other parts we are about to remove on top of it. The boiler is located below, which may be still hot. Be careful not to burn yourself.
\end{minipage}
\hfill
\begin{minipage}[t]{0.4\linewidth}
	\vspace{0pt}
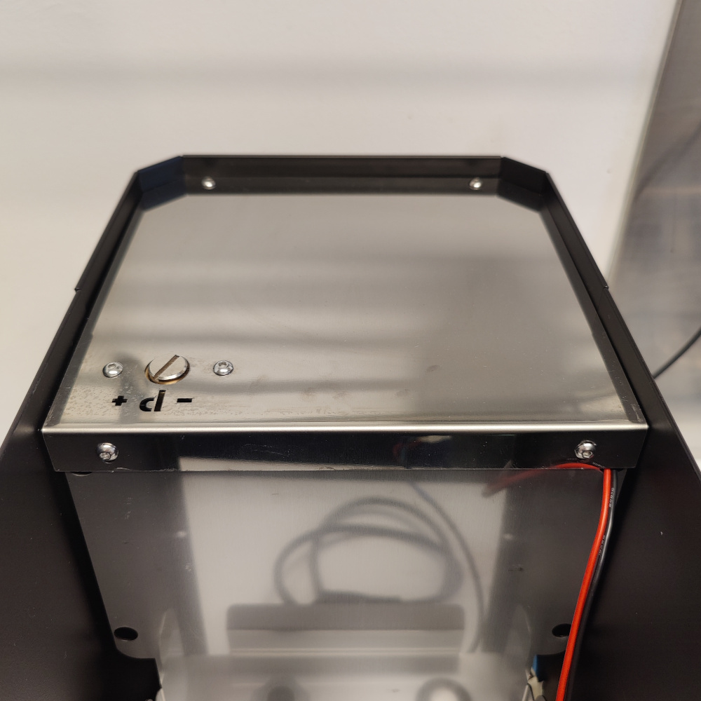
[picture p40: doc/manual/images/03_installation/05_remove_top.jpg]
	
\end{minipage}

\subsubsection{Removing the dividerplate}
\label{sec:dividerplate}
\begin{minipage}[t]{0.5\linewidth}
	\vspace{0pt}
	Next, we have to remove the divider that separates the water-tank from the electronics. This is a bit tricky, since the screws are located at the bottom of the machine. There are two screws that need to be removed, highlighted in the first picture. If you are alone, I recommend positioning the machine at the edge of the table and slightly tilting it, until you can unscrew it from the bottom (shown in second picture). Once the screws on both sides are out, you also need to unscrew the water intake (third picture). Afterwards, carefully slide the dividerplate out. Place it on some soft surface (e.g. a towel) to avoid scratches. Do NOT place any other parts we are about to remove on top of it. Do not damage any of the waterlines or cables! The intake may have some remaining water, take a piece of papertowel to drain it (fourth picture).
\end{minipage}
\hfill
\begin{minipage}[t]{0.4\linewidth}
	\vspace{0pt}
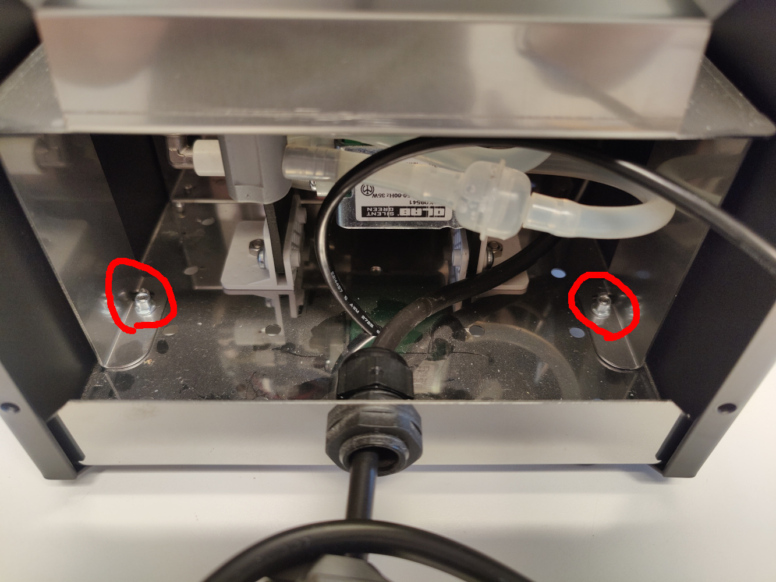
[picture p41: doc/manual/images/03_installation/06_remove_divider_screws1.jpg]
	
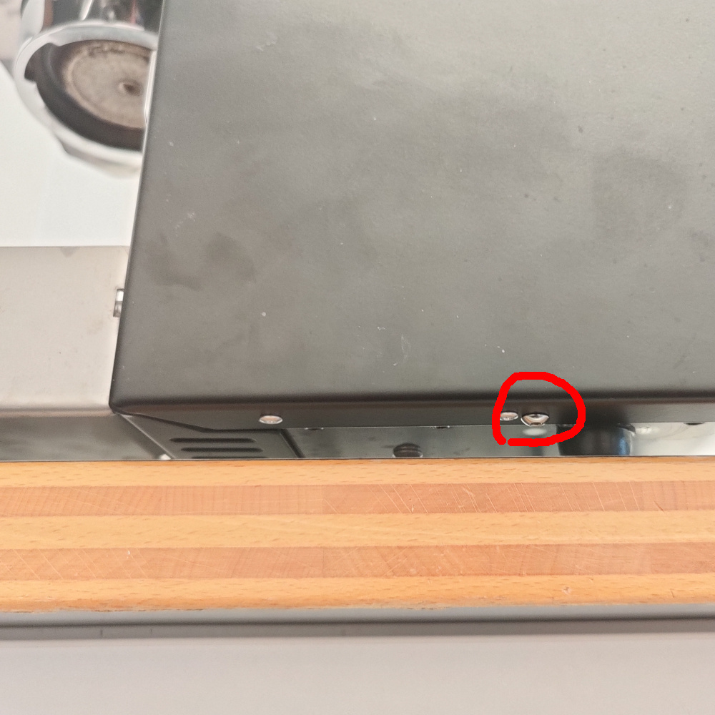
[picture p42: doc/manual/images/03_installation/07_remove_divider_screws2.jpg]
	
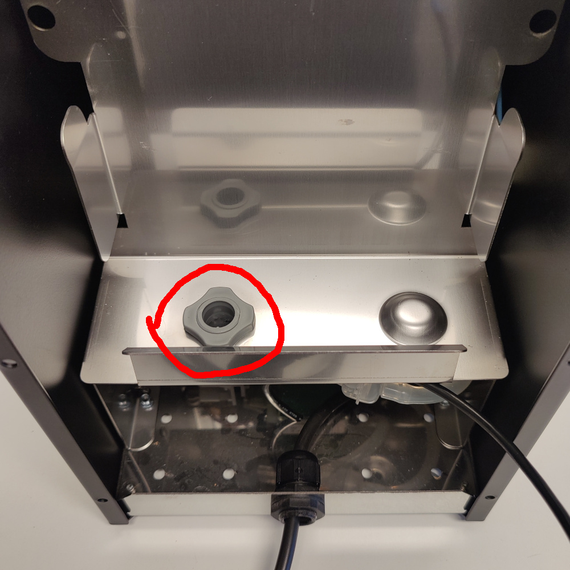
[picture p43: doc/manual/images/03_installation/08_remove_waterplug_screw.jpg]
	
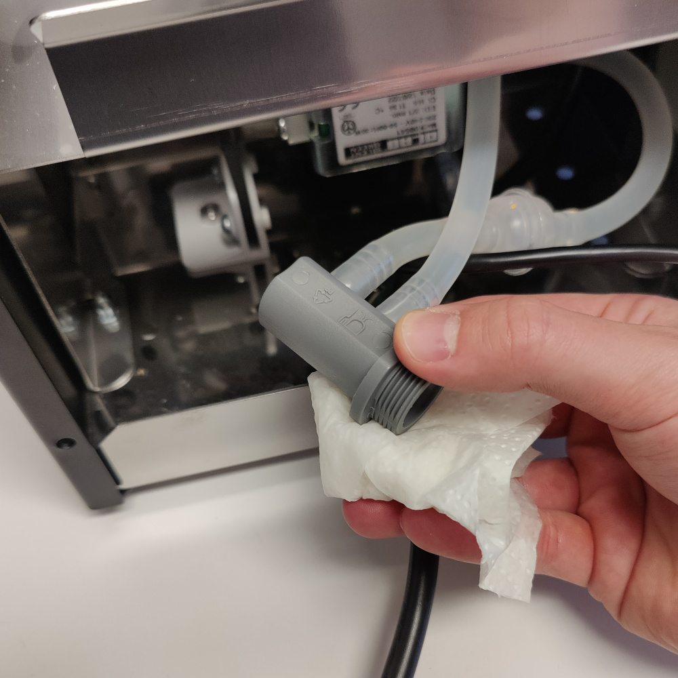
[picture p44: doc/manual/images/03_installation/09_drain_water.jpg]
	
\end{minipage}

\subsubsection{Pulling through the display cable}
\begin{minipage}[t]{0.5\linewidth}
	\vspace{0pt}
	Take the display cable and push the end with the two 2-Pin connectors through one of the holes at the bottom of the machine. The connectors need to be passed through one after the other in order to fit through the hole. You can plug in the display unit at the other end and stick it to the location you would like to have it. That way, you know exactly how much cable you need to leave hanging out.
\end{minipage}
\hfill
\begin{minipage}[t]{0.4\linewidth}
	\vspace{0pt}
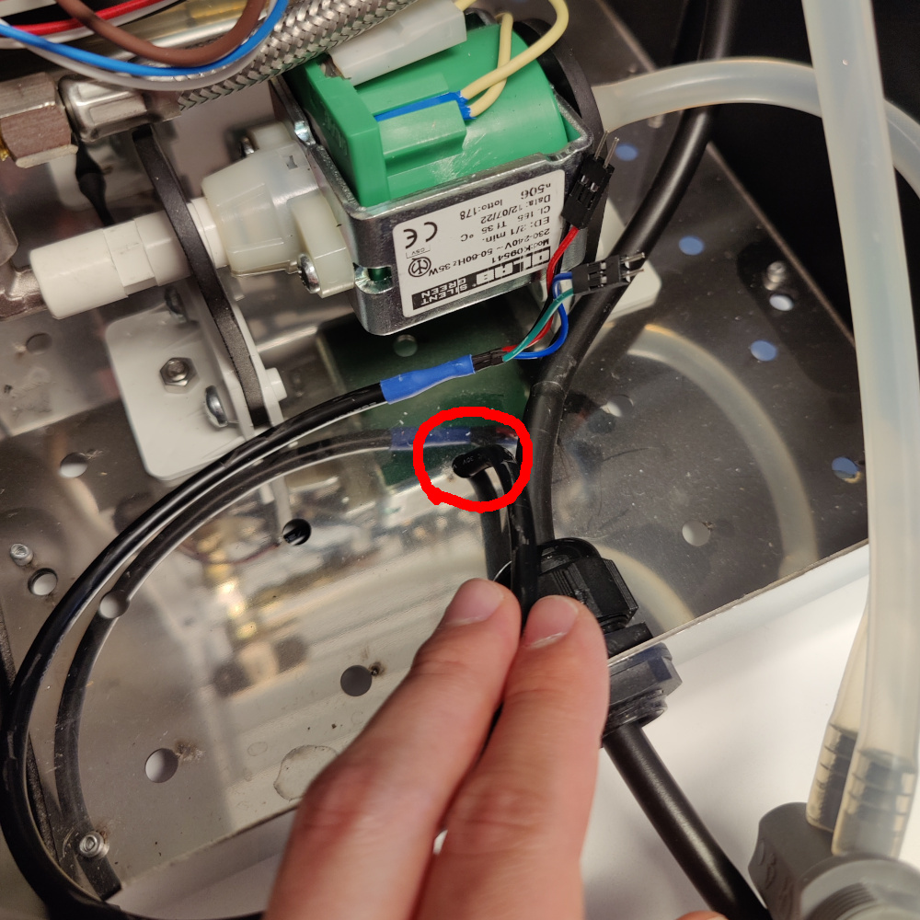
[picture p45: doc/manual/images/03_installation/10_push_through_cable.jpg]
	
\end{minipage}

\subsubsection{Connecting the power supply}
\begin{minipage}[t]{0.5\linewidth}
	\vspace{0pt}
	\textbf{Check again that the machine is unplugged!} In this step, we have to connect the power supply to the mains voltage, so ideally there shouldn't be any live wires. Connecting the power supply can be done in a non-destructive way by building adapters for the plugs used in your machine. The method I went with is destructive and splices open the power cord. To do this, unscrew the black cap at the power cord inlet to be able to pull the power cord through the hole and give you better access to the cord. Mark about 5cm with two pieces of tape (first image). Remove the outer isolation between the two pieces of tape (second image). \textbf{Be careful not to damage the inner isolation of the three wires}. There is a blue, brown and green-yellow cable inside. Cut the blue and brown wire in the middle. \textbf{Do NOT cut the yellow-green wire. Its purpose is to prevent the machine from killing you.} Strip some of the isolation off and reconnect them using splicing connectors (third picture). I am using WAGO connectors, which need 11mm if isolation removed from the end. Use the third port in each connector to connect the power supply (fourth picture).
\end{minipage}
\hfill
\begin{minipage}[t]{0.4\linewidth}
	\vspace{0pt}
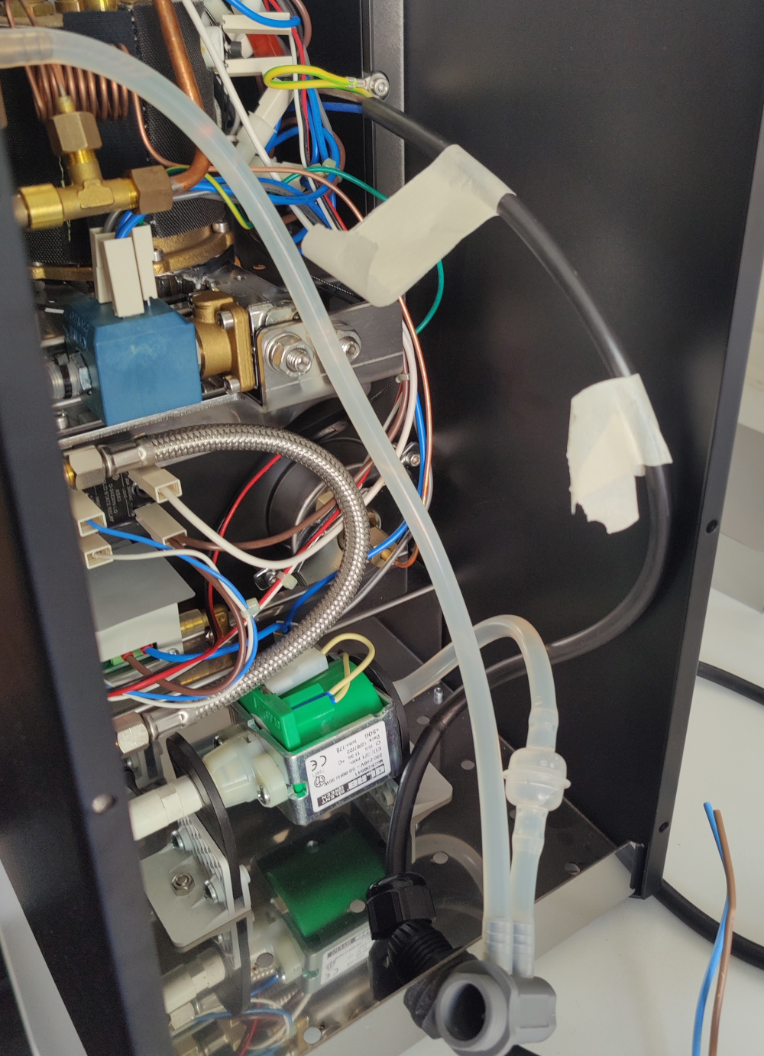
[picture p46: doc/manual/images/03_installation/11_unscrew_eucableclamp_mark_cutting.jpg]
	
	
	
	
\end{minipage}

\subsubsection{Installing the power supply and dividerplate}
\begin{minipage}[t]{0.5\linewidth}
	\vspace{0pt}
	Use the double-sided tape to stick the power supply to the side of the machine like shown in the picture. If you are unsure where exactly to position it, take the dividerplate and topplate to figure out how much space you have and where to install the power supply without interference. Reinstall the dividerplate by performing the steps in Section~\ref{sec:dividerplate} in reverse.
\end{minipage}
\hfill
\begin{minipage}[t]{0.4\linewidth}
	\vspace{0pt}
	
\end{minipage}

\subsubsection{Installing the topplate}
\begin{minipage}[t]{0.5\linewidth}
	\vspace{0pt}
	Take the wire harness and thread the 2-Pin JST-XH connector of the wire harness through the hole in the divider plate. Connect it to the power supply. Reinstall the topplate by performing the steps in Section~\ref{sec:topplate} in reverse. Do not fully tighten all screws of the topplate directly! First, screw all of them in loose, then one by one tighten them to avoid any tension building up across the plate. Make sure the two wires running through the hole aren't pinched.
\end{minipage}
\hfill
\begin{minipage}[t]{0.4\linewidth}
	\vspace{0pt}
	
	
\end{minipage}

\subsubsection{Connection check}
\begin{minipage}[t]{0.5\linewidth}
	\vspace{0pt}
	Connect The 4-Pin Dupont of the wire harness and the two 2-Pin Duponts from the display cable as shown in the first image. Again, the TX of the display has to be connected to the RX of the level sensor and vice-versa. Your color coding might be different. If not done already, connect the display unit to the display cable outside of the machine. Place the water-tank lid with the level sensor on the topplate, with the sensor facing the topplate. Connect the level sensor to the wire harness. Plug in the machine. Verify that the display shows a 99 percent blue indicator. If the indicator is still orange with a question mark, the display could not communicate with the level sensor. In that case, doublecheck the RX-TX connection and all other plugs. If everything works, unplug the machine again and unplug the levelsensor.
\end{minipage}
\hfill
\begin{minipage}[t]{0.4\linewidth}
	\vspace{0pt}
	
	
\end{minipage}

\subsubsection{Cable management and backplate}
\begin{minipage}[t]{0.5\linewidth}
	\vspace{0pt}
	I recommend wrapping some isolation tape around the Dupont connectors and sticking the to the upper edge of the machine with double-sided tape as shown in the picture. Make sure you are able to pull the 4-Pin JST-XH connector of the wire harness for the level-sensor higher out of the machine (this will make it easier to remove the level sensor when the machine is assembled). Afterwards, reinstall the backplate by performing the steps of section \ref{sec:backplate} in reverse. Be careful not to damage any cables.
\end{minipage}
\hfill
\begin{minipage}[t]{0.4\linewidth}
	\vspace{0pt}
	
\end{minipage}

\subsubsection{Finishline}
\begin{minipage}[t]{0.5\linewidth}
	\vspace{0pt}
	Reinstall the water-tank. Pull the 4-Pin JST-XH connector out of the machine while doing so (first picture). Make sure the water-tank doesn't sit on any other cables. Reconnect the level sensor (second picture). Push the JST-XH connector plug and any excess sensor cables under the ledge of the water-tank to hide them (third picture). The lid should close as normal, without any cable visible. That's it. You have successfully installed the mod! Congratulations!
\end{minipage}
\hfill
\begin{minipage}[t]{0.4\linewidth}
	\vspace{0pt}
	
	
	
\end{minipage}

\end{document}

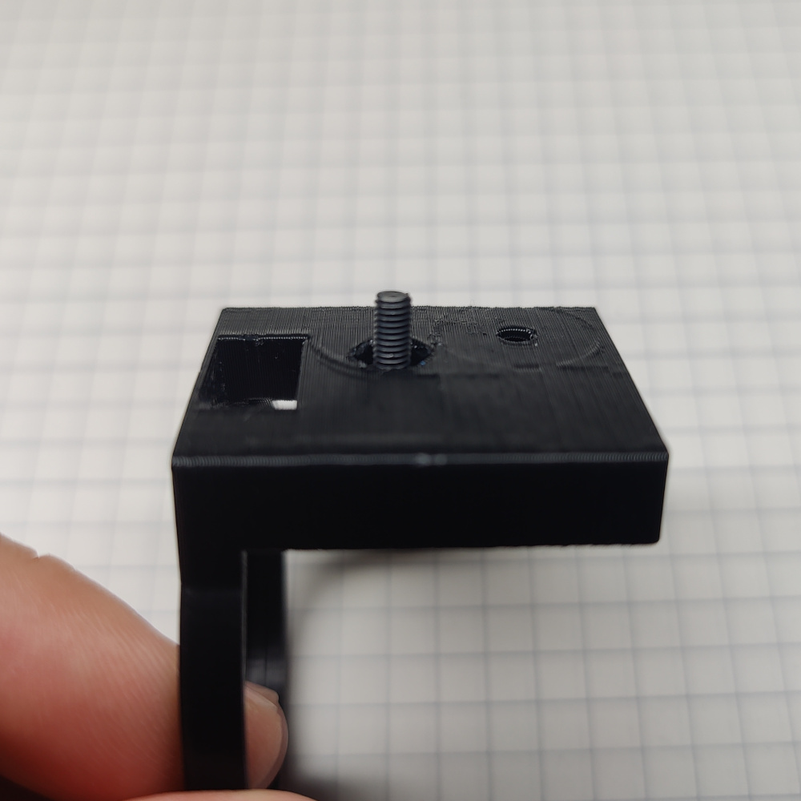
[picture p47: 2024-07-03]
doc/manual/images/01_displayunit/10_check_nut.jpg

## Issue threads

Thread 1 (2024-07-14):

A0221AT version sensor

MK7GolfR, 2024-07-14:
I received a sensor version A0221AT which seems to be slightly different and am getting no signal output from it.  Digging a little I found that  "This sensor is an A0221AT, which is actually a serial controled DYP-A02T. This modules requires a positive pulse on its RX pin to start measuring. About 60ms later it will then proved the measurement on its TX pin."   Does your code send this pulse to start measuring? or can it be made compatible?

lspr98, 2024-07-14:
Hey,

no, the code does not send this pulse as the sensor variant listed in the BOM does not require it. If you want to send a high pulse during sensor initialization you can adapt the init function in [src/levelsensor.cpp](https://github.com/lspr98/profitec-go-waterlevel-shottimer/blob/main/src/levelsensor.cpp) as follows:

```
void init() {
        // Send HIGH pulse for 60ms to levelsensor
        gpio_set_dir(PIN_LEVELSENSOR_TX, 1);
        gpio_put(PIN_LEVELSENSOR_TX, 1);
        sleep_ms(60);
        gpio_put(PIN_LEVELSENSOR_TX, 0);
        // Route HW UART1 to given RX,TX pins.
        gpio_set_function(PIN_LEVELSENSOR_TX, GPIO_FUNC_UART);
        gpio_set_function(PIN_LEVELSENSOR_RX, GPIO_FUNC_UART);
}
```

I couldn't find a datasheet for the "A0221AT" nor an entry in the DFRobot wiki, so I am assuming a 60ms HIGH pulse is sufficient based on your question. Also, I don't have your sensor to test anything, so I can't guarantee that this will work. After adapting the code, you need to reflash it via USB.

You could also double check that the TX pin of the display unit is connected to the RX pin of the level sensor and the RX pin of the display unit is connected to the TX pin of the level sensor. Does the display unit show an orange ring as depicted in the manual?

MK7GolfR, 2024-07-14:
Thanks for the reply, the display still shows the orange ring when connected and I tried swapping the Tx / Rx pins back and forth with no success.  I suspect [this sensor from Amazon ](https://www.amazon.ca/gp/product/B0CFFTS71Y/)must be slightly different and require the pulse to get it started.  I will try to adapt the code and retry, thanks for your help!

MK7GolfR, 2024-07-15:
I tried adding your adaptions but so far no success unfortunately.
I was able to find some more info regarding this module and it's quirks:

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

lspr98, 2024-07-15:
Hey,

thanks for the additional information. If I interpret that correctly, the distance measurement for your sensor version has to be actively triggered. To set the UART data format as described in your answer, another adjustment in the init function in [src/levelsensor.cpp](https://github.com/lspr98/profitec-go-waterlevel-shottimer/blob/main/src/levelsensor.cpp) is required:

```
void init() {
        // 8 data bits, one stop bit and no parity
        uart_set_format(uart1, 8, 1, UART_PARITY_NONE);
        // Send HIGH pulse for 60ms to levelsensor
        gpio_set_dir(PIN_LEVELSENSOR_TX, 1);
        gpio_put(PIN_LEVELSENSOR_TX, 1);
        sleep_ms(60);
        gpio_put(PIN_LEVELSENSOR_TX, 0);
        // Route HW UART1 to given RX,TX pins.
        gpio_set_function(PIN_LEVELSENSOR_TX, GPIO_FUNC_UART);
        gpio_set_function(PIN_LEVELSENSOR_RX, GPIO_FUNC_UART);
}
```

Next, you need to adjust the for loop in the getDistance function, also in [src/levelsensor.cpp](https://github.com/lspr98/profitec-go-waterlevel-shottimer/blob/main/src/levelsensor.cpp) to send something over UART to trigger a measurement:

```
// Try to read a valid value LEVEL_N_RETRY times
for(uint16_t i=0; i<LEVEL_N_RETRY; i++) {

    // Send something to trigger falling edge on sensor RX
    uart_putc(uart1, '\n');

    // 100 ms timeout to wait for sensor response
    sleep_ms(100);

    // Recieved no new data. Retry by continuing with next loop
    if(!uart_is_readable(uart1)) {
        continue;
    }

    // New data was recieved. According to the sensor wiki, there should be 4 bytes.
    // https://wiki.dfrobot.com/_A02YYUW_Waterproof_Ultrasonic_Sensor_SKU_SEN0311
    uart_read_blocking(uart1, serialData, 4);

    // Check if header byte is correct
    if(serialData[0]==0xff) {
        // Calculate checksum
        int checksum = (serialData[0]+serialData[1]+serialData[2])&0x00FF;
        // Check if checksum matches
        if(checksum == serialData[3]) {
            // Clip distance to [minDistanceMM, maxDistanceMM] range
            float distance = (serialData[1]<<8)+serialData[2];
            if(distance > LEVEL_MAX_DIST_MM) {
                distance = LEVEL_MAX_DIST_MM;
            } else if(distance < LEVEL_MIN_DIST_MM){
                distance = LEVEL_MIN_DIST_MM;
            }
            // Close uart
            uart_deinit(uart1);
            return distance;
        }
    }
}
```

In the snippet above, **uart_putc** sends a newline character to the levelsensor via UART as described in your answer and **sleep_ms** waits 100ms for the sensor to respond. Also, if you happen to find a datasheet for your sensor version, let me know.

MK7GolfR, 2024-07-15:
Success!
The code adaptions worked perfectly and the sensor now reports back the level.
I wasn't able to find a Datasheet but luckily the info provided from these other buyers proved useful.

lspr98, 2024-07-16:
Glad to hear that :). If that solved your problem, please feel free to close the issue.

Closed 2024-07-16.

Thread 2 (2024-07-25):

Waveshare RP2040 - LCD 0.99

mlc8446, 2024-07-25:
Hi there!

I've got a WaveShare RP2040 LCD 0.99B about that I wanted to use for this project: https://www.waveshare.com/wiki/RP2040-LCD-0.99-B

Main reason was to try out a more 'foolproof' way of building this mod for people who can understand the build, but not want to 3D print, solder pins together, etc. I thought this might be good alternative to the original idea.

I tested out the code, it builds and flashes correctly onto the board, but I'm just getting a white/wavy screen on the RP2040. From what I can see, the RP2040 you used initially in your build appears to be pretty identical to the one I've got (main difference is the size) but I'm not seeing any obvious reasons throughout the whole code why it displays a white screen rather than the orange circle/timer.

From what I can see, it does go onto the board correctly - as if I leave it for a few seconds it turns off, then wakes upon movement.

Any chance you can think of a reason why your code wouldn't be suitable for this board? I've looked at the connections, pins, colours etc but couldn't find anything obvious. Any help would be amazing thanks!

mlc8446, 2024-07-25:
Nevermind! I missed a pin that was different from your original build - I've more or less accounted for the different screensize etc so just moving the ring to the centre. Will post a copy of the modified sections if anyone else wants a copy

mintyman, 2024-10-08:
> Nevermind! I missed a pin that was different from your original build - I've more or less accounted for the different screensize etc so just moving the ring to the centre. Will post a copy of the modified sections if anyone else wants a copy

I'm interested in going down the route of RP2040-LCD-0.99-B to limit soldering etc. Can you provide more details on changes to the code / build ?

Closed 2024-07-25.

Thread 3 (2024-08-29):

Translating source code from Waveshare RP2040-LCD-1.28 to RP2040-Touch-LCD-1.28

fable-coltish, 2024-08-29:
I inadvertently purchased the [TOUCH version](https://www.waveshare.com/wiki/RP2040-Touch-LCD-1.28) of the RP2040-LCD-1.28 and found that the pin-out assignments on this version of the board are not the same as on the [non-touch version](https://www.waveshare.com/wiki/RP2040-LCD-1.28).

When I initially flashed the firmware (without making any changes) the display would not output anything. The display would blink at the initial flash and then the LCD would remain all dark, with the backlight on. After going through the documentation for the touch board I managed to get the screen to work by changing the SPI configuration in the file -> "include / [display.h](https://github.com/lspr98/profitec-go-waterlevel-shottimer/blob/main/include/display.h)" on Line 13:

From -> `#define LCD_RST_PIN     (12)`
To -> `#define LCD_RST_PIN     (13)`

For reference, this is based on the LCD mappings on the [board schematics pdf](https://files.waveshare.com/upload/3/3c/RP2040-Touch-LCD-1.28.pdf). All other mappings for the LCD are correct in the existing source code.

The code change worked and upon a new firmware flash the display starts up as expected. The display currently shows the orange ring with a question mark indicating a missing fill-level sensor, and the shot timer starts after shaking the device for more than two seconds.

For the TX and RX inputs for the water level sensor, I managed to reassign the GPIO pins to GPIO16 and GPIO17 in the source code. There are two required changes:

1. In the file -> "include / [levelsensor.h](https://github.com/lspr98/profitec-go-waterlevel-shottimer/blob/main/include/levelsensor.h)" change the GPIO assignments on line 4 and 5:

From:
`#define PIN_LEVELSENSOR_TX 4u`
`#define PIN_LEVELSENSOR_RX 5u`

To:
`#define PIN_LEVELSENSOR_TX 16u`
`#define PIN_LEVELSENSOR_RX 17u`

2. In the file -> "src / [levelsensor.cpp](https://github.com/lspr98/profitec-go-waterlevel-shottimer/blob/main/src/levelsensor.cpp) change any mention of `uart1` to `uart0` in the entire document.

Those two changes should allow the Waveshare RP2040-Touch-LCD-1.28 to work as intended by the author. If the display still shows the initial display with no change (i.e. orange circle with question mark), switch your RX / TX wires around and power cycle the processor. The working state should show a blue circle with a percentage sign at the bottom and a number in the middle.

-------------------------------------------------------------------------------------
**Attempted but failed alternative solution:**

As an alternative, I also attempted to use the original source code by soldering wires to the GPIO 4 and GPIO 5 connectors on the board as seen on the schematic. More specifically, the #2 pads on headers P4 and P5 seen here:

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

However, the processor does not seem to recognise the water level sensor through this method. I suspect that this is because the GPIOs are hidden behind the resistors and diodes as shown in the schematics.

Any Arduino / RP2040 experts out there to provide some tips? I can test it out on my board.

Closed 2024-08-29.

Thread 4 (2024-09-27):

Battery power option?

SteveNewhouse, 2024-09-27:
Might it be possible to adapt this for a battery-powered option in case there are ppl less comfortable tapping the machine power?  Could something like this work? https://www.amazon.com/gp/product/B099P95JPH/ref=ewc_pr_img_2?smid=AYZMETEBRR587&psc=1

lspr98, 2024-09-28:
Hey Steve,

it probably would work, but you will be on your own to try that out. The system draws around 1W when the display is on, so your power supply should at least be able to handle that (AA batteries should be able capable of more). If you have a look at the wiring diagram, you simply have to replace the mains-powered power supply with your power supply.

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

I don't know how much the system is drawing on average when in standby, hence I can't give you an estimate on how often you will have to swap batteries. Another possible option would be to use an old phone charger with a USB-A port and an old USB-A cable (that way you don't need to open your machine or handle mains voltage and you don't need to replace batteries).

Going with a battery-powered solution just replaces one problem with another. Instead of having to look after the fill-level of the espresso machine, you now have to look after the batteries of the fill-level sensor. But it's open-source and you can build whatever you want out of it ;)

SteveNewhouse, 2024-10-01:
Thank you

lspr98, 2024-10-11:
Hey Steve,

USB-C is tricky, since often there is some sort of communication between the charger and the device necessary to decide on the output voltage. It could very well be a voltage issue, as you pointed out correctly.

Did you per chance measure the voltage across the red (+5V) and black (GND) cables while the other end is plugged in? If you don't get 5V it may be an issue with the charger not getting any feedback from the device and hence not delivering any output voltage. In that case you may need to solder an additional sensing-resistor to the wires (but I am really not an expert regarding USB-C).

You could also measure the voltage across the two cables while the display is powered via the USB-C port on the display (make sure the other end of the cable that you soldered to the display is unplugged!). If you then measure 5V across the two solder joints where the red and black cables are soldered to, you know that you got the correct pins.

In all cases, take care that you never connect the display from both sides simultaneously to a power source, otherwise you may ruin the display or your devices.

SteveNewhouse, 2024-10-12:
Yeah- using a simple USB-A cable it works!  Thank you for all your help!

Closed 2024-10-12.

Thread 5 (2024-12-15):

Error reading sensor when powered by power supply. Works when plugging into via USB-C port

hosfordryan, 2024-12-15:
Hi, not too experienced with electronics so asking here for some help. Feel free to close if this isn't the right place.

I've got everything wired up but am getting an error on the display reading the distance sensor when it's all powered by the 5v power supply (using a separate 5v power supply instead of tapping into the machine's power). However, it works when I disconnect the power supply 5v and GND from the connection to the display, but keep it connected to the distance sensor while plugging the display in to my computer via USB-C.

Any ideas why this might be happening? I assumed that the issue was with power to the distance sensor, but that seems to be working. When I do just use the external 5v power supply, the display runs and shows "?", so it seems like it's being powered properly.

I'm using a 5v 1a power supply. [This one specifically](https://www.amazon.com/dp/B09W8X9VGK?ref=ppx_yo2ov_dt_b_fed_asin_title)

hosfordryan, 2024-12-16:
No idea why it was behaving the way it was, but following the solution of [this issue](https://github.com/lspr98/profitec-go-waterlevel-shottimer/issues/1) resolved my issue too.

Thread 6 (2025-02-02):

Cannot flash firmware to Waveshare RP2040-LCD-1.28 on Ubuntu

mattkwiecien, 2025-02-02:
Hi, I'm working on step 1.1.19 of the guide where we plug in the display and flash the firmware onto the device.

I have VS Code set up, PlatformIO set up, cloned the repo, plugged in my display unit via USB to my PC, and the device is working and showing coordinates.

Without changing anything, when I run the upload I get

```
 *  Executing task: platformio run --target upload

Processing pico (platform: https://github.com/maxgerhardt/platform-raspberrypi.git; board: waveshare_rp2040_lcd_1_28; framework: arduino)
------------------------------------------------------------------------------------------------------------------------
Verbose mode can be enabled via `-v, --verbose` option
CONFIGURATION: https://docs.platformio.org/page/boards/raspberrypi/waveshare_rp2040_lcd_1_28.html
PLATFORM: Raspberry Pi RP2040 (1.15.0+sha.39b9039) > RP2040 LCD 1.28
HARDWARE: RP2040 133MHz, 256KB RAM, 2MB Flash
DEBUG: Current (blackmagic) External (blackmagic, cmsis-dap, jlink, picoprobe, raspberrypi-swd)
PACKAGES:
 - framework-arduinopico @ 1.40300.0+sha.e16c459
 - tool-mklittlefs-rp2040-earlephilhower @ 5.100300.230216 (10.3.0)
 - tool-openocd-rp2040-earlephilhower @ 5.140200.240929 (14.2.0)
 - tool-picotool-rp2040-earlephilhower @ 5.140200.240929 (14.2.0)
 - toolchain-rp2040-earlephilhower @ 5.140200.240929 (14.2.0)
Flash size: 2.00MB
Sketch size: 2.00MB
Filesystem size: 0.00MB
PSRAM size: 0.00MB
Maximium Sketch size: 2093056 EEPROM start: 0x101ff000 Filesystem start: 0x101ff000 Filesystem end: 0x101ff000
LDF: Library Dependency Finder -> https://bit.ly/configure-pio-ldf
LDF Modes: Finder ~ chain, Compatibility ~ soft
Found 70 compatible libraries
Scanning dependencies...
Dependency Graph
|-- Font
|-- QMI8658
Building in release mode
Compiling .pio/build/pico/FrameworkArduinoBootloader/boot2_w25q16jvxq_4_padded_checksum.S.o
Compiling .pio/build/pico/src/counter.cpp.o
Compiling .pio/build/pico/src/display.cpp.o
Compiling .pio/build/pico/src/graphics.cpp.o
Compiling .pio/build/pico/src/interpolator.cpp.o
Compiling .pio/build/pico/src/levelsensor.cpp.o
Compiling .pio/build/pico/src/main.cpp.o
Compiling .pio/build/pico/src/ringindicator.cpp.o
Compiling .pio/build/pico/src/serialutils.cpp.o
Compiling .pio/build/pico/src/statusindicator.cpp.o
Generating linkerscript /home/matt/repos/profitec-go-waterlevel-shottimer/.pio/build/pico/memmap_default.ld
Compiling .pio/build/pico/lib040/QMI8658/QMI8658.cpp.o
Compiling .pio/build/pico/FrameworkArduino/BluetoothDebug.cpp.o
Compiling .pio/build/pico/FrameworkArduino/Bootsel.cpp.o
Compiling .pio/build/pico/FrameworkArduino/CoreMutex.cpp.o
Archiving .pio/build/pico/lib040/libQMI8658.a
Indexing .pio/build/pico/lib040/libQMI8658.a
Compiling .pio/build/pico/FrameworkArduino/FS.cpp.o
Compiling .pio/build/pico/FrameworkArduino/PIOProgram.cpp.o
Compiling .pio/build/pico/FrameworkArduino/RP2040Support.cpp.o
Compiling .pio/build/pico/FrameworkArduino/RP2040USB.cpp.o
Compiling .pio/build/pico/FrameworkArduino/SerialPIO.cpp.o
Compiling .pio/build/pico/FrameworkArduino/SerialUART.cpp.o
Compiling .pio/build/pico/FrameworkArduino/SerialUSB.cpp.o
Compiling .pio/build/pico/FrameworkArduino/StackThunk.cpp.o
Compiling .pio/build/pico/FrameworkArduino/Tone.cpp.o
Compiling .pio/build/pico/FrameworkArduino/WMath.cpp.o
Compiling .pio/build/pico/FrameworkArduino/_freertos.cpp.o
Compiling .pio/build/pico/FrameworkArduino/api/Common.cpp.o
Compiling .pio/build/pico/FrameworkArduino/api/IPAddress.cpp.o
Compiling .pio/build/pico/FrameworkArduino/api/PluggableUSB.cpp.o
Compiling .pio/build/pico/FrameworkArduino/api/Print.cpp.o
Compiling .pio/build/pico/FrameworkArduino/api/Stream.cpp.o
Compiling .pio/build/pico/FrameworkArduino/api/String.cpp.o
Compiling .pio/build/pico/FrameworkArduino/cyw43_wrappers.cpp.o
Compiling .pio/build/pico/FrameworkArduino/delay.cpp.o
Compiling .pio/build/pico/FrameworkArduino/libb64/cdecode.cpp.o
Compiling .pio/build/pico/FrameworkArduino/libb64/cencode.cpp.o
Compiling .pio/build/pico/FrameworkArduino/lock.cpp.o
Compiling .pio/build/pico/FrameworkArduino/lwip_wrap.cpp.o
Compiling .pio/build/pico/FrameworkArduino/main.cpp.o
Compiling .pio/build/pico/FrameworkArduino/malloc-lock.cpp.o
Compiling .pio/build/pico/FrameworkArduino/posix.cpp.o
Compiling .pio/build/pico/FrameworkArduino/psram.cpp.o
Compiling .pio/build/pico/FrameworkArduino/rp2350-memcpy.S.o
Compiling .pio/build/pico/FrameworkArduino/sdkoverride/btstack_flash_bank.cpp.o
Compiling .pio/build/pico/FrameworkArduino/sdkoverride/inet_chksum.cpp.o
Compiling .pio/build/pico/FrameworkArduino/sdkoverride/newlib_interface.c.o
Compiling .pio/build/pico/FrameworkArduino/sdkoverride/pico_bootsel_via_double_reset.c.o
Compiling .pio/build/pico/FrameworkArduino/stdlib_noniso.cpp.o
Compiling .pio/build/pico/FrameworkArduino/wiring_analog.cpp.o
Compiling .pio/build/pico/FrameworkArduino/wiring_digital.cpp.o
Compiling .pio/build/pico/FrameworkArduino/wiring_private.cpp.o
Compiling .pio/build/pico/FrameworkArduino/wiring_pulse.cpp.o
Compiling .pio/build/pico/FrameworkArduino/wiring_shift.cpp.o
Archiving .pio/build/pico/libFrameworkArduino.a
Indexing .pio/build/pico/libFrameworkArduino.a
Linking .pio/build/pico/firmware.elf
Generating UF2 image
picotool uf2 convert -t elf ".pio/build/pico/firmware.elf" ".pio/build/pico/firmware.uf2"
Retrieving maximum program size .pio/build/pico/firmware.elf
Flash size: 2.00MB
Sketch size: 2.00MB
Filesystem size: 0.00MB
PSRAM size: 0.00MB
Maximium Sketch size: 2093056 EEPROM start: 0x101ff000 Filesystem start: 0x101ff000 Filesystem end: 0x101ff000
Checking size .pio/build/pico/firmware.elf
Advanced Memory Usage is available via "PlatformIO Home > Project Inspect"
RAM:   [          ]   3.7% (used 9704 bytes from 262144 bytes)
Flash: [=         ]   5.4% (used 113384 bytes from 2093056 bytes)
Building .pio/build/pico/firmware.bin
Configuring upload protocol...
AVAILABLE: blackmagic, cmsis-dap, jlink, mbed, picoprobe, picotool, raspberrypi-swd
CURRENT: upload_protocol = mbed
Trying to reset Pico into bootloader mode...
Forcing reset using 1200bps open/close on port /dev/ttyACM0
Looking for upload disk...
Error: Please specify `upload_port` for environment or use global `--upload-port` option.
For some development platforms it can be a USB flash drive (i.e. /media/<user>/<device name>)
*** [upload] Explicit exit, status 1
============================================== [FAILED] Took 5.35 seconds ==============================================
```

I then ran `sudo dmesg -w` in the terminal, unplugged my device and re-plugged it back in to find which device it is:
```
[  639.451869] usb 1-3: USB disconnect, device number 11
[  651.214120] usb 1-3: new full-speed USB device number 12 using xhci_hcd
[  651.360135] usb 1-3: New USB device found, idVendor=2e8a, idProduct=000a, bcdDevice= 1.00
[  651.360154] usb 1-3: New USB device strings: Mfr=1, Product=2, SerialNumber=3
[  651.360162] usb 1-3: Product: Pico
[  651.360169] usb 1-3: Manufacturer: Raspberry Pi
[  651.360175] usb 1-3: SerialNumber: E6635C469F5F9F2F
[  651.370364] cdc_acm 1-3:1.0: ttyACM0: USB ACM device
```

Using that information, I specified both in the platformio.ini and in the lower panel of VSCode that the device I want to upload to is `ttyACM0`.

Retrying the upload I get
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
mattkwiecien, 2025-02-02:
I checked out the PlatformIO Serial Monitor which stated [Errno 13] could not open port /dev/ttyACM0: [Errno 13] Permission denied: '/dev/ttyACM0'.

Ran a `sudo chmod 666 /dev/ttyACM0` and then re-ran the upload.  Sadly it still failed.  This time the device shut off though.  Upon unplugging and re-plugging in, it still works with the original firmware.

```
 *  Executing task: platformio run --target upload --upload-port /dev/ttyACM0

Processing pico (platform: https://github.com/maxgerhardt/platform-raspberrypi.git; board: waveshare_rp2040_lcd_1_28; framework: arduino)
------------------------------------------------------------------------------------------------------------------------
Verbose mode can be enabled via `-v, --verbose` option
CONFIGURATION: https://docs.platformio.org/page/boards/raspberrypi/waveshare_rp2040_lcd_1_28.html
PLATFORM: Raspberry Pi RP2040 (1.15.0+sha.39b9039) > RP2040 LCD 1.28
HARDWARE: RP2040 133MHz, 256KB RAM, 2MB Flash
DEBUG: Current (blackmagic) External (blackmagic, cmsis-dap, jlink, picoprobe, raspberrypi-swd)
PACKAGES:
 - framework-arduinopico @ 1.40300.0+sha.e16c459
 - tool-mklittlefs-rp2040-earlephilhower @ 5.100300.230216 (10.3.0)
 - tool-openocd-rp2040-earlephilhower @ 5.140200.240929 (14.2.0)
 - tool-picotool-rp2040-earlephilhower @ 5.140200.240929 (14.2.0)
 - toolchain-rp2040-earlephilhower @ 5.140200.240929 (14.2.0)
Flash size: 2.00MB
Sketch size: 2.00MB
Filesystem size: 0.00MB
PSRAM size: 0.00MB
Maximium Sketch size: 2093056 EEPROM start: 0x101ff000 Filesystem start: 0x101ff000 Filesystem end: 0x101ff000
LDF: Library Dependency Finder -> https://bit.ly/configure-pio-ldf
LDF Modes: Finder ~ chain, Compatibility ~ soft
Found 70 compatible libraries
Scanning dependencies...
Dependency Graph
|-- Font
|-- QMI8658
Building in release mode
Retrieving maximum program size .pio/build/pico/firmware.elf
Flash size: 2.00MB
Sketch size: 2.00MB
Filesystem size: 0.00MB
PSRAM size: 0.00MB
Maximium Sketch size: 2093056 EEPROM start: 0x101ff000 Filesystem start: 0x101ff000 Filesystem end: 0x101ff000
Checking size .pio/build/pico/firmware.elf
Advanced Memory Usage is available via "PlatformIO Home > Project Inspect"
RAM:   [          ]   3.7% (used 9704 bytes from 262144 bytes)
Flash: [=         ]   5.4% (used 113384 bytes from 2093056 bytes)
Configuring upload protocol...
AVAILABLE: blackmagic, cmsis-dap, jlink, mbed, picoprobe, picotool, raspberrypi-swd
CURRENT: upload_protocol = mbed
Trying to reset Pico into bootloader mode...
Forcing reset using 1200bps open/close on port /dev/ttyACM0
Looking for upload disk...
Using manually specified: /dev/ttyACM0
Uploading .pio/build/pico/firmware.bin
*** [upload] /dev/ttyACM0/firmware.uf2: No such file or directory
============================================== [FAILED] Took 3.06 seconds ==============================================
```

mattkwiecien, 2025-02-02:
RESOLVED!

After this step above

> Ran a sudo chmod 666 /dev/ttyACM0 and then re-ran the upload. Sadly it still failed. This time the device shut off though. Upon unplugging and re-plugging in, it still works with the original firmware.

I realized the device was being added as a external USB drive with path `/media/matt/RPI-RP2`.

I added the following to the `platformio.ini` file `upload_port = /media/matt/RPI-RP2`.  Re-ran the upload, and it worked.

Looks like you need to have the device in this USB drive mode in order to flash the firmware.  Maybe good to update the documentation with that!

Closed 2025-03-25.

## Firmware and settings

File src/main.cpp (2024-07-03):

#include <Arduino.h>
#include <pico/rand.h>
#include <graphics.h>
#include <counter.h>
#include <serialutils.h>
#include <ringindicator.h>
#include <interpolator.h>
#include <Roboto_Light20pt7b.h>
#include <SoftwareSerial.h>
#include <QMI8658.h>
#include <display.h>
#include <levelsensor.h>
#include <statusindicator.h>
#include <config.h>

// UI elements
Counter counter;
Interpolator interpolator;
RingIndicator ring;
StatusIndicator status;

// Initial ring indicator color
uint16_t currRingColor = RING_COLOR_OK;
// Fill level percentage tracker
float currPerc, targetPerc = 0;
// Sleep states
bool isAwake, isVibrating, isVibratingPrev = false;
// Timing
long tLastVibration = 0;
long loopStart, loopEnd = 0;
// Vibration logging
float acc_xyz[IMU_N_SAMPLES][3], acc_mean_xyz[3], acc_std_xyz[3];


/**
 * Checks for vibrations by reading samples from the accelerometer, 
 * calculating the standard deviation of these samples and comparing it
 * to a threshold. 
 */
bool checkVibration() {
  // Read Sensor IMU_N_SAMPLES times
  for(int i=0; i<IMU_N_SAMPLES; i++) {
    // Get current XYZ accelerations
    QMI8658_read_acc_xyz(acc_xyz[i]);
    // Wait for a short time before reading next sample
    sleep_ms(IMU_READ_DELAY_MS);
  }

  // Calculate mean for each axis
  for(int i=0; i<3; i++) {
    acc_mean_xyz[i] = 0;
    for(int j=0; j<IMU_N_SAMPLES; j++) {
      acc_mean_xyz[i] += acc_xyz[j][i];
    }
    acc_mean_xyz[i] /= IMU_N_SAMPLES;
  }

  // Calculate std for each axis
  for(int i=0; i<3; i++) {
    acc_std_xyz[i] = 0;
    for(int j=0; j<IMU_N_SAMPLES; j++) {
      acc_std_xyz[i] += pow(acc_xyz[j][i] - acc_mean_xyz[i], 2);
    }
    acc_std_xyz[i] = sqrtf(acc_std_xyz[i] / IMU_N_SAMPLES);

    // Check if threshold is exceeded
    if(acc_std_xyz[i] > WAKE_THRESH) {
      return true;
    }
  }

  return false;
}


/**
 * Routine that shows and increases a timer each second if a continuous
 * vibration is detected. Finishes once the vibration stops for a second.
 */
void timerRoutine(long tStart) {
  // Time passed since timer was started
  long tPassed = millis() - tStart;
  // Approximate time needed to check for vibration
  long tVibeCheck = IMU_N_SAMPLES*IMU_READ_DELAY_MS;
  status.showStatus(StatusIndicatorState::TIMER, STATUS_COLOR);
  counter.update(((float)tPassed)/TIMER_INCREMENT_MS, COUNTER_COLOR);
  // Outer loop keeps the timer running, performing second-wise updates
  while(true) {
    bool isVibrating = false;
    // Inner loop keeps checking if the machine is still vibrating while a full second hasn't passed
    while(true) {
      // Perform vibration check
      isVibrating = checkVibration();
      // Update last vibration time if applicable
      if(isVibrating) tLastVibration = millis();
      // Calculate remaining time to next full second
      long tDiff = (millis() - tStart);
      tDiff = (floor((float)tDiff/TIMER_INCREMENT_MS)+1)*TIMER_INCREMENT_MS - tDiff;
      // Check if enough time for another vibecheck is left or a vibration was detected
      if(isVibrating || tVibeCheck >= tDiff) {
        // Wait remaining time to full second if applicable
        if(tDiff > 0) sleep_ms(tDiff);
        break;
      }
    }
    // Break timer loop if no vibration was detected in the past second
    if(!isVibrating) break;

    // Update timer
    tPassed = millis() - tStart;
    counter.update(((float)tPassed)/TIMER_INCREMENT_MS, COUNTER_COLOR);
  }
}

/**
 * Routine that tries to read a valid filllevel. If a valid value
 * is read, the filllevel is displayed after an animation.
 * If no valid value is read, an error screen is shown
 */
void levelRoutine(float transitionTime) {
  // Try to get fill level
  targetPerc = LevelSensor::getFillPercentage();
  
  // Choose ring color based on percentage
  if(targetPerc > LEVEL_BAD_PERC) {
    currRingColor = RING_COLOR_OK;
  } else {
    currRingColor = RING_COLOR_BAD;
  }

  if(targetPerc > -1) {
    status.showStatus(StatusIndicatorState::LEVEL, STATUS_COLOR);
    counter.update(currPerc, COUNTER_COLOR);
    ring.updatePrec(currPerc, currRingColor);
  } else {
    // Couldn't read filllevel. Show error state
    status.showStatus(StatusIndicatorState::ERROR, STATUS_COLOR);
    counter.hide();
    ring.updatePrec(100, currRingColor);
  }

  // Gradually wakeup display
  for(int i=0; i < 100; i++) {
    Display::setBrightness(i);
    sleep_ms(DIM_STEP_DELAY_MS);
  }

  if(targetPerc > -1) {
    // Transition
    interpolator.setFromTo(currPerc, targetPerc, transitionTime);
    while(!interpolator.next(currPerc)) {
        loopStart = millis();
        ring.updatePrec(currPerc, currRingColor);
        counter.update(currPerc, COUNTER_COLOR);
        loopEnd = millis();
        if(loopEnd-loopStart < FRAME_TIME_MS) {
            sleep_ms(FRAME_TIME_MS - (loopEnd-loopStart));
        }
    }
  }
}

/**
 * Wakes up the system by triggering the level routine and resetting the current fill percentage.
 */
void systemWake() {
  // Reset level
  currPerc = 0;
  isAwake = true;
  levelRoutine(TRANSITION_TIME_LONG_MS);
  
}


/**
 * Puts the system to sleep state by dimming the display and hiding UI elements
 * Note: The MCU is not actually put to sleep, just the display is turned off.
 */
void systemSleep() {
  // Gradually dim display
  for(int i=99; i > -1; i--) {
    Display::setBrightness(i);
    sleep_ms(DIM_STEP_DELAY_MS);
  }

  // Hide UI elements
  counter.hide();
  status.hide();
  ring.hide();

  // Wipe display
  Display::clear(BLACK);

  isAwake = false;
}


void setup() {

    Serial.begin(9600);

    // Initialize display
    Display::init();
    Display::clear(BLACK);

    // Initialize IMU
    QMI8658_init();

    // Initialize level sensor
    LevelSensor::init();

    // Update ring limits to make space for status symbol at the bottom
    ring.setLimits(0.2*PI, 1.8*PI);

    systemWake();

}

void loop() {

    isVibrating = checkVibration();
    if(isVibrating && !isVibratingPrev) tLastVibration = millis();

    if(!isAwake && isVibrating) {
      // System is sleeping and vibrating
      systemWake();
    } else if(isVibrating) {
      // System is awake and vibrating
      // Wait for timer trigger delay
      sleep_ms(TIMER_TRIGGER_DELAY_MS);
      // Start timer if enabled and still vibrating
      if(ENABLE_TIMER && checkVibration()) {
        timerRoutine(tLastVibration);
        // Vibration stopped, go back to show fill level
        levelRoutine(TRANSITION_TIME_SHORT_MS);
      }
      
    } else if(isAwake && ((millis() - tLastVibration) > SLEEP_TIMEOUT_MS)) {
      // Sleep due to timeout
      systemSleep();
    }

    isVibratingPrev = isVibrating;
}

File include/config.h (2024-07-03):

#ifndef _CONFIG_H
#define _CONFIG_H

// *******************************
//    Waterlevel sensor settings
// *******************************
// Profitec Go water reservoir is ~25cm deep
// The intake for the pump sticks out about 2cm
// The sensor sticks around ~2cm into the tank
// So at 25cm - 2cm - 2cm = 21cm = 210mm, the pump starts sucking air (0% fill level)
#define LEVEL_MAX_DIST_MM 210
// DF-A02YYUW sensor has a blind distance of 3cm = 30mm
#define LEVEL_MIN_DIST_MM 30
// Number of times to try reading a value from the sensor
#define LEVEL_N_RETRY 10
// Delay between two consecutive read attempts
#define LEVEL_READ_DELAY_MS 10
// Percentage value below which the ring changes color from OK to BAD
#define LEVEL_BAD_PERC 25

// *******************************
//       IMU sensor settings
// *******************************
// Number of samples to read from IMU
#define IMU_N_SAMPLES 10
// Delay between two consecutive reads
#define IMU_READ_DELAY_MS 10
// Minimum required standard deviation among samples to detect a vibration
#define WAKE_THRESH 0.5

// *******************************
//         Timer settings
// *******************************
// If you don't need the timer, you can disable it.
#define ENABLE_TIMER true
// How much milliseconds one increment of the counter needs
// For a precise shot time measurement, 1000ms should be used for a full second
// My Profitec GO seems to count a bit faster than 1000ms
#define TIMER_INCREMENT_MS 975
// The timer is started when the system is awake and a vibration is detected
// The trigger delay defines how many milliseconds the system has to vibrate
// while being awake until the timer is activated. This prevents the timer
// from starting when e.g. the portafilter is removed/inserted
#define TIMER_TRIGGER_DELAY_MS 2000


// *******************************
//         Counter settings
// *******************************
// Center point position of counter in pixels
#define COUNTER_CENTER_X 120
#define COUNTER_CENTER_Y 120
// Color of counter
#define COUNTER_COLOR WHITE

// *******************************
//     RingIndicator settings
// *******************************
// Center point position of ring-indicator in pixels
#define RING_CENTER_X 120
#define RING_CENTER_Y 120
// Radius of ring-indicator in pixels
#define RING_RADIUS 100
// Width of ring-indicator in pixels
#define RING_WIDTH 15
// Color of ring-indicator if fill level percentage > LEVEL_BAD_PERC
#define RING_COLOR_OK CYAN
// Color of ring-indicator if fill level percentage <= LEVEL_BAD_PERC
#define RING_COLOR_BAD BRRED

// *******************************
//    StatusIndicator settings
// *******************************
// Center point position of status-indicator in pixels
#define STATUS_CENTER_X 120
#define STATUS_CENTER_Y 215
// Color of status-indicator
#define STATUS_COLOR WHITE

// *******************************
//       Animation settings
// *******************************
// Target frame time for ring animation in milliseconds
#define FRAME_TIME_MS 20
// Animation time for ring-indicator when system wakes up
#define TRANSITION_TIME_LONG_MS 3000
// Animation time for ring-indicator after timer ends
#define TRANSITION_TIME_SHORT_MS 1500

// *******************************
//        Display settings
// *******************************
// Rotation of display
// Depending on the side at which the sensor is mounted, a different rotation
// value is required:
// Right:       90
// Left:        270
// Top:         0
// Bottom:      180
#define ROTATION 270
// Time after which the display goes dark when no vibration was detected
#define SLEEP_TIMEOUT_MS 60000
// Delay between dimming steps. Dimming is performed from 100 to 0 in decrements of 1.
#define DIM_STEP_DELAY_MS 1



#endif

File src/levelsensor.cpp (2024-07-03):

#include <levelsensor.h>
#include <serialutils.h>
#include <config.h>

namespace LevelSensor {
    
    void flush() {
        // Empty buffer by reading from it until it is empty.
        while(uart_is_readable(uart1)) {
            uart_getc(uart1);
        }
    }

    void init() {
        // Route HW UART1 to given RX,TX pins.
        gpio_set_function(PIN_LEVELSENSOR_TX, GPIO_FUNC_UART);
        gpio_set_function(PIN_LEVELSENSOR_RX, GPIO_FUNC_UART);
    }

    float getFillPercentage() {
        // Read raw distance
        float distance = getDistance();
        
        // Return -1 if there was an error reading
        if(distance < 0) return distance;

        // Convert to fill level to percentage. Note that the value has to be reversed since
        // LEVEL_MIN_DIST_MM indicates a full tank (100%) and LEVEL_MAX_DIST_MM an empty tank (0%)
        float perc = (1 - (distance - LEVEL_MIN_DIST_MM)/(LEVEL_MAX_DIST_MM - LEVEL_MIN_DIST_MM)) * 100;

        return perc;
    }

    float getDistance() {
        // Initialize uart
        uart_init(uart1, 9600);
        sleep_ms(100);

        // Clear old data from serial buffer
        flush();

        // Try to read a valid value LEVEL_N_RETRY times
        for(uint16_t i=0; i<LEVEL_N_RETRY; i++) {
            
            // Small timeout to wait for new data from sensor
            sleep_ms(LEVEL_READ_DELAY_MS);

            // Recieved no new data. Retry by continuing with next loop
            if(!uart_is_readable(uart1)) {
                continue;
            }
            
            // New data was recieved. According to the sensor wiki, there should be 4 bytes.
            // https://wiki.dfrobot.com/_A02YYUW_Waterproof_Ultrasonic_Sensor_SKU_SEN0311
            uart_read_blocking(uart1, serialData, 4);

            // Check if header byte is correct
            if(serialData[0]==0xff) {
                // Calculate checksum
                int checksum = (serialData[0]+serialData[1]+serialData[2])&0x00FF;
                // Check if checksum matches
                if(checksum == serialData[3]) {
                    // Clip distance to [minDistanceMM, maxDistanceMM] range
                    float distance = (serialData[1]<<8)+serialData[2];
                    if(distance > LEVEL_MAX_DIST_MM) {
                        distance = LEVEL_MAX_DIST_MM;
                    } else if(distance < LEVEL_MIN_DIST_MM){
                        distance = LEVEL_MIN_DIST_MM;
                    }
                    // Close uart
                    uart_deinit(uart1);
                    return distance;
                }
            }
        }

        // Close uart
        uart_deinit(uart1);
        // failed to read a valid value.
        sout.err() <= "Failed to read from level sensor";
        return -1;
    }
}

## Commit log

2024-07-03 migration to github
    [Frame v14.stl, Lid v10.stl]
2024-07-03 added missing bom item
2024-07-03 updated information in readme, adjusted reading settings for waterlevel sensor
2024-07-03 reinitialize waterlevel sensor on each read
